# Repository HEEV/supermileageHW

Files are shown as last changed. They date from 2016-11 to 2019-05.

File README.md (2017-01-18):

# Cedarville Supermileage HW
Kicad files for PCBs on the Ceaderville Supermileage team. Also includes wiring diagrams and schematics
drawn in Kicad.
#Contents of Folders
* Library Folders
    * EllicottSamuel: Files I made before supermileage which were too much work to port over.
    *  parts_library: Files dedicated for the supermileage team.

* Project Folders
    * can_sensor: PCB to connect generic sensors to the CANBus.
    * current_sensor: Three port current sensor board that connects to the CANBus. 
	Current sensor chip is the Allegro ACS710.
    * pressure_sensor: Pressure sensor board, output as an analog voltage. 
	Supported sensors are the Honeywell ASDX100A24R, Honeywell HSCDRR004MD, and the
	AllSensors G4V-Mini.
    * Sting: wiring diagrams and schematics for Sting produced using Kicad.
        * wiring diagrams: kicad files for the wiring diagrams.
        * schematics: kicad files for the schematics.
    * Urbie: wiring diagrams and schematics for Urbie produced using Kicad.
    	* wiring diagrams: kicad files for the wiring diagrams.
        * schematics: kicad files for the schematics.

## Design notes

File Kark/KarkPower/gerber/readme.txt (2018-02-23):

readme.txt - KarkPower folder contents

KarkPower.drl            - Drill File
KarkPower-drl_map.pdf    - Drill Map File
KarkPower-B-Cu.gbl       - Back Copper
KarkPower-B-SilkS.gbo    - Back Silk
KarkPower-F-Cu.gtl       - Front Copper
KarkPower-F-SilkS.gto    - Front Silk
KarkPower-Edge-Cuts.gm1  - Board Edge

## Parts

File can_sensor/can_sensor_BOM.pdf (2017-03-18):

can_sensor_BOM

Page 1

Reference | Value | Footprint | Count | FootprintLib | Distributor | PN
C15;C5;C17;C13;C11 | 1uf | C_0603_HandSoldering | 5 Capacitors_SMD | | Mouser | 80-C0603C105K8P
C6;C16;C9;C10;C2;C8;C4;C18;C14;C12 | 0.1uf | C_0603_HandSoldering | 10 Capacitors_SMD
C7;C3;C1;C19;C20 | 10uf | C_0603_HandSoldering | 5 Capacitors_SMD | | Mouser | 80-C0603C105K8P
D1;D2;D3;D4 | hi_v | SOD-123 | 4 Diodes_SMD
D7 | reverse | SOD-123 | 1 Diodes_SMD | | Mouser | 581-SD1206S040S0R5
D8 | LED1 | LED_0603 | 1 LEDs
D9 | LED2 | LED_0603 | 1 LEDs
P1 | IO1 | Molex-duraClick-4conn | 1 User_Connectors | | Mouser | 538-53261-0471
P2 | IO2 | Molex-duraClick-4conn | 1 User_Connectors | | Mouser | 538-53261-0471
P4 | CONN_01X03 | Pin_Header_Straight_1x03 | 1 Pin_Headers
P5 | USB | USB_Micro-B | 1 Connect | | Mouser | 649-10118194-0001LF
P6 | CAN_IN | Molex-duraClick-4conn | 1 User_Connectors | | Mouser | 538-53261-0471
P7 | CAN_OUT | Molex-duraClick-4conn | 1 User_Connectors | | Mouser | 538-53261-0471
R1;R9;R8 | 100K | R_0603_HandSoldering | 3 Resistors_SMD | | Mouser | 71-CRCW0603-100K-E3
R10;R11;R12 | 120R | R_0603_HandSoldering | 3 Resistors_SMD | | Mouser | 71-CRCW0603-120-E3
R6;R5;R3;R2 | R | R_0603_HandSoldering | 4 Resistors_SMD
SW1 | RESET | SW_SPST_FSMSM | 1 Buttons_Switches_SMD
SW2 | BOOT | SW_SPST_FSMSM | 1 Buttons_Switches_SMD
U1 | NJM2870F0 | SOT-23-5 | 1 TO_SOT_Packages_SMD | | Mouser | 513-NJM2870F05-TE2
U2 | MIC5317 | SOT-23-5 | 1 TO_SOT_Packages_SMD | | Mouser | 998-MIC5317-3.3YM5TR
U3 | STM32F042C6 | TQFP-48_7x7mm_Pitch0.5mm | 1 Housings_QFP
U4 | mcp2562 | SOIC-8-N | 1 SMD_Packages | | Mouser | 579-MCP2562-E/SN

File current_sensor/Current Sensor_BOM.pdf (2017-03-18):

Current Sensor_BOM

Page 1

Reference | Value | Footprint | Count | FootprintLib | Distributor | PN
C1;C8;C14 | 1nf | C_0603_HandSoldering | 3 Capacitors_SMD
C23;C25;C21;C19 | 1uf | C_0603_HandSoldering | 4 Capacitors_SMD | | Mouser | 80-C0603C105K8P
C4;C5;C6;C3;C11;C16;C10;C13;C24;C18;C17;C26;C22;C20 | 0.1uf | C_0603_HandSoldering | 14 Capacitors_SMD
C7;C12 | 10uf | C_0603_HandSoldering | 2 Capacitors_SMD
C9;C15;C2 | 4.7nf | C_0603_HandSoldering | 3 Capacitors_SMD
D1 | LED1 | LED-3MM | 1 LEDs
D2 | LED2 | LED-3MM | 1 LEDs
D4;D3;D5;D7;D6;D8 | D_Schottky_Small | SOD-123 | 6 Diodes_SMD | | Mouser | 512-SS14FL
P1 | CAN_IN | Molex-duraClick-4conn | 1 User_Connectors | | Mouser | 538-502352-0400
P10;P11;P12 | CONN_02X03 | Pin_Header_Straight_2x03 | 3 Pin_Headers
P2 | CAN_OUT | Molex-duraClick-4conn | 1 User_Connectors | | Mouser | 538-502352-0400
P3 | DuraClik-5 | Molex-duraClick-5conn | 1 User_Connectors | | Mouser | 538-502352-0501
P4;P5;P6 | Ultra-Fit | Molex-UltraFit-2p | 3 Supermileage | | Mouser | 538-172310-2102
P7 | CONN_01X03 | Pin_Header_Straight_1x03 | 1 Pin_Headers
P8 | USB | USB_Micro-B | 1 Connect | | Mouser | 649-10118194-0001LF
P9 | CONN_01X02 | Pin_Header_Straight_1x02 | 1 Pin_Headers
Q1 | Reverse | SOT-23_Handsoldering | 1 TO_SOT_Packages_SMD | | Mouser | 863-NTR3A30PZT1G
R1;R3;R5 | 1k | R_0603_HandSoldering | 3 Resistors_SMD
R10;R22;R24 | 8k2 | R_0603_HandSoldering | 3 Resistors_SMD
R12;R18;R20 | 4k7 | R_0603_HandSoldering | 3 Resistors_SMD
R14;R7 | 100K | R_0603_HandSoldering | 2 Resistors_SMD | | Mouser | 71-CRCW0603-100K-E3
R15;R16;R17 | 120R | R_0603_HandSoldering | 3 Resistors_SMD | | Mouser | 71-CRCW0603-120-E3
R2;R4;R6 | 2k | R_0603_HandSoldering | 3 Resistors_SMD
R8;R26;R28 | 18k | R_0603_HandSoldering | 3 Resistors_SMD | | Mouser
R9;R11;R13;R27;R23;R19;R29;R25;R21 | 1k3 | R_0603_HandSoldering | 9 Resistors_SMD
SW1 | RESET | SW_PUSH_6mm | 1 Buttons_Switches_ThroughHole | | Mouser | SKHHPPA010
SW2 | BOOT | SW_PUSH_6mm | 1 Buttons_Switches_ThroughHole | | Mouser | SKHHPPA010
U1;U3;U5 | ACS710 | DIP-16-SchmartBoard | 3 Supermileage
U2 | NJM2870F0 | SOT-23-5 | 1 TO_SOT_Packages_SMD | | Mouser | 513-NJM2870F05-TE2
U4 | MIC5317 | SOT-23-5 | 1 TO_SOT_Packages_SMD | | Mouser | 998-MIC5317-3.3YM5TR
U6 | STM32F042C6 | TQFP-48_7x7mm_Pitch0.5mm | 1 Housings_QFP | | Mouser | 511-STM32F042C6T6
U7 | mcp2562 | SOIC-8-N | 1 SMD_Packages | | Mouser | 579-MCP2562-E/SN

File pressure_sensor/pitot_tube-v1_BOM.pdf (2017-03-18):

pitot_tube-v1_BOM

Page 1

Reference | Value | Footprint | Count | FootprintLib | Distributor
C1;C3;C4;C5;C7 | 0.1uf | C_0603_HandSoldering | 5 Capacitors_SMD | | Mouser
C2;C6;C8 | 10uf | C_0603_HandSoldering | 3 Capacitors_SMD
P1 | CONN_01X04 | Molex-duraClick-4conn | 1 User_Connectors
P2 | CONN_01X03 | Pin_Header_Straight_1x03 | 1 Pin_Headers
Q1;Q2 | Q_PMOS_GSD | SOT-23_Handsoldering | 2 TO_SOT_Packages_SMD
R1 | 1k | R_0603_HandSoldering | 1 Resistors_SMD
R2 | 2k | R_0603_HandSoldering | 1 Resistors_SMD
U1 | HSCDRR004MD | DIP-8 | 1supermileage
U2 | NJM2870F0 | SOT-23-5 | 1 TO_SOT_Packages_SMD
U3 | ASDX100A24R | ASDX100A24R | 1supermileage
U4 | G4V-MINI | Socket_Strip_Straight_1x04 | 1 Socket_Strips
W1;W2;W3;W4 | Mount | MountingHole_2.2mm_M2 | 4 Mounting_Holes

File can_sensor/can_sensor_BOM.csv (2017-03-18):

Reference | Value | Footprint | Count | Datasheet | FootprintLib | Distributor | PN
U4 | mcp2562 | SOIC-8-N | 1 |  | SMD_Packages | Mouser | 579-MCP2562-E/SN
U2 | MIC5317 | SOT-23-5 | 1 |  | TO_SOT_Packages_SMD | Mouser | 998-MIC5317-3.3YM5TR
C7;C3;C1;C19;C20 | 10uf | C_0603_HandSoldering | 5 |  | Capacitors_SMD | Mouser | 80-C0603C105K8P
C6;C16;C9;C10;C2;C8;C4;C18;C14;C12 | 0.1uf | C_0603_HandSoldering | 10 |  | Capacitors_SMD
C15;C5;C17;C13;C11 | 1uf | C_0603_HandSoldering | 5 |  | Capacitors_SMD | Mouser | 80-C0603C105K8P
D7 | reverse | SOD-123 | 1 |  | Diodes_SMD | Mouser | 581-SD1206S040S0R5
P6 | CAN_IN | Molex-duraClick-4conn | 1 |  | User_Connectors | Mouser | 538-53261-0471
P7 | CAN_OUT | Molex-duraClick-4conn | 1 |  | User_Connectors | Mouser | 538-53261-0471
P1 | IO1 | Molex-duraClick-4conn | 1 |  | User_Connectors | Mouser | 538-53261-0471
P2 | IO2 | Molex-duraClick-4conn | 1 |  | User_Connectors | Mouser | 538-53261-0471
R10;R11;R12 | 120R | R_0603_HandSoldering | 3 |  | Resistors_SMD | Mouser | 71-CRCW0603-120-E3
D8 | LED1 | LED_0603 | 1 |  | LEDs
D9 | LED2 | LED_0603 | 1 |  | LEDs
P5 | USB | USB_Micro-B | 1 |  | Connect | Mouser | 649-10118194-0001LF
SW2 | BOOT | SW_SPST_FSMSM | 1 |  | Buttons_Switches_SMD
SW1 | RESET | SW_SPST_FSMSM | 1 |  | Buttons_Switches_SMD
U1 | NJM2870F0 | SOT-23-5 | 1 |  | TO_SOT_Packages_SMD | Mouser | 513-NJM2870F05-TE2
R1;R9;R8 | 100K | R_0603_HandSoldering | 3 |  | Resistors_SMD | Mouser | 71-CRCW0603-100K-E3
P4 | CONN_01X03 | Pin_Header_Straight_1x03 | 1 |  | Pin_Headers
D1;D2;D3;D4 | hi_v | SOD-123 | 4 |  | Diodes_SMD
R6;R5;R3;R2 | R | R_0603_HandSoldering | 4 |  | Resistors_SMD
U3 | STM32F042C6 | TQFP-48_7x7mm_Pitch0.5mm | 1 |  | Housings_QFP

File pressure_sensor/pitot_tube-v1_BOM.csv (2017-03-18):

Reference | Value | Footprint | Count | Datasheet | FootprintLib | Distributor
U1 | HSCDRR004MD | DIP-8 | 1 |  | supermileage
P1 | CONN_01X04 | Molex-duraClick-4conn | 1 |  | User_Connectors
C1;C3;C4;C5;C7 | 0.1uf | C_0603_HandSoldering | 5 |  | Capacitors_SMD | Mouser
C2;C6;C8 | 10uf | C_0603_HandSoldering | 3 |  | Capacitors_SMD
W1;W2;W3;W4 | Mount | MountingHole_2.2mm_M2 | 4 |  | Mounting_Holes
U2 | NJM2870F0 | SOT-23-5 | 1 |  | TO_SOT_Packages_SMD
P2 | CONN_01X03 | Pin_Header_Straight_1x03 | 1 |  | Pin_Headers
R1 | 1k | R_0603_HandSoldering | 1 |  | Resistors_SMD
R2 | 2k | R_0603_HandSoldering | 1 |  | Resistors_SMD
Q1;Q2 | Q_PMOS_GSD | SOT-23_Handsoldering | 2 |  | TO_SOT_Packages_SMD
U3 | ASDX100A24R | ASDX100A24R | 1 |  | supermileage
U4 | G4V-MINI | Socket_Strip_Straight_1x04 | 1 |  | Socket_Strips

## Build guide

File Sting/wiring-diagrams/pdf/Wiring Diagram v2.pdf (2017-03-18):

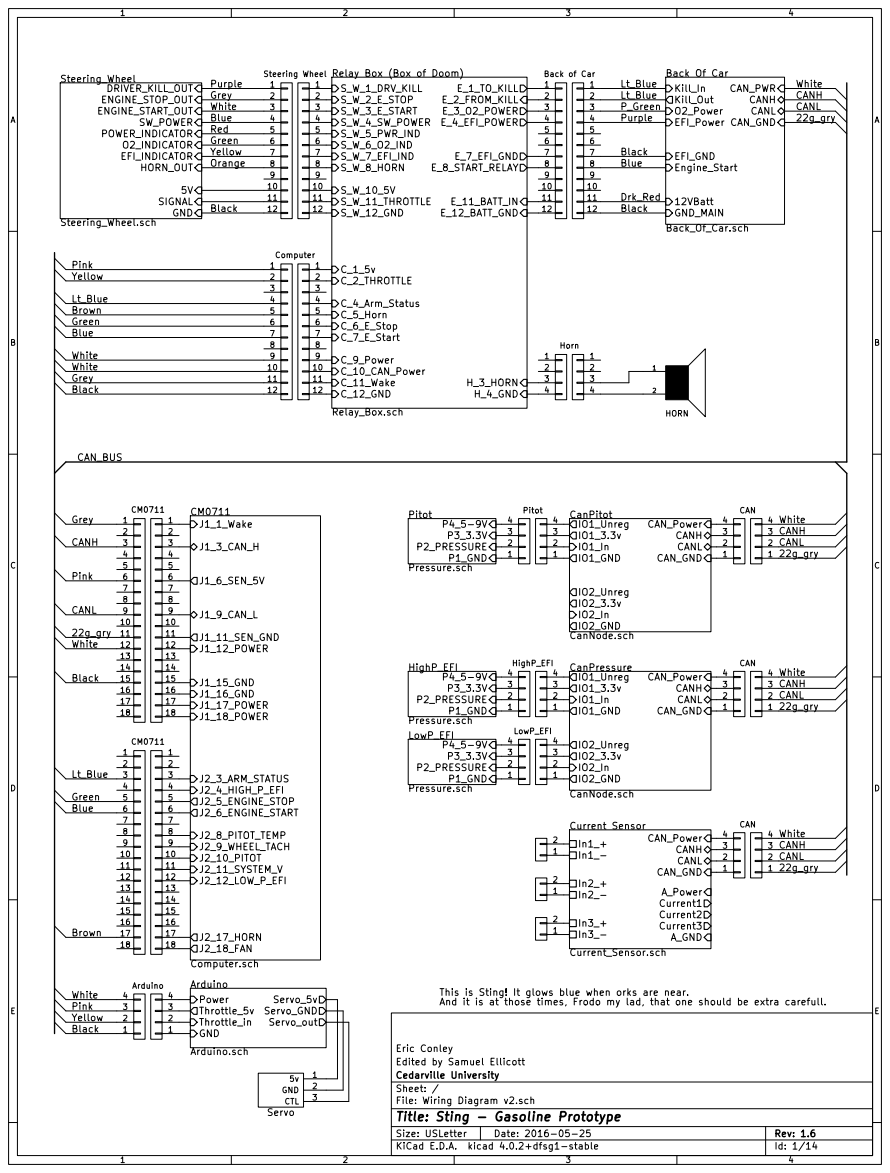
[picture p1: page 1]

2 | | 2 | | 2 | | 2 | Lt_Blue
3 | | 3 | | 3 | | 3 P_Green

C_10_CAN_Power Grey Pink Lt_Blue Brown Black White White Green Blue Yellow Grey White

10 | 2
11 | 3 | 3
12 | 4

12
13

This is Sting! It glows blue when orks are near.
And it is at those times, Frodo my lad, that one should be extra carefull.

Eric Conley
Edited by Samuel Ellicott
File: Wiring Diagram v2.sch Sheet: / Cedarville University

Id: 1/14 Title: Sting - Gasoline Prototype

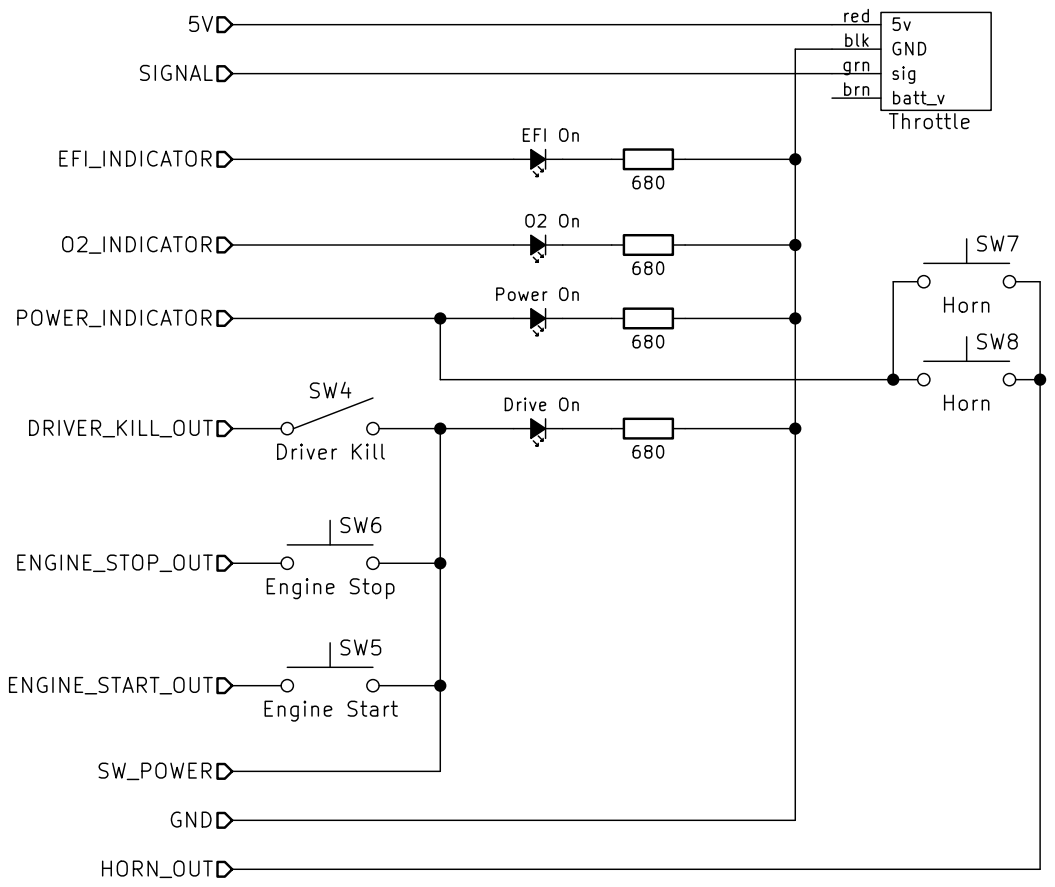
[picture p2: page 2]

Eric Conley
Edited by Samuel Ellicott
Cedarville University
Sheet: /Steering_Wheel/
File: Steering_Wheel.sch
Id: 2/14 Title: Sting - Gasoline Prototype

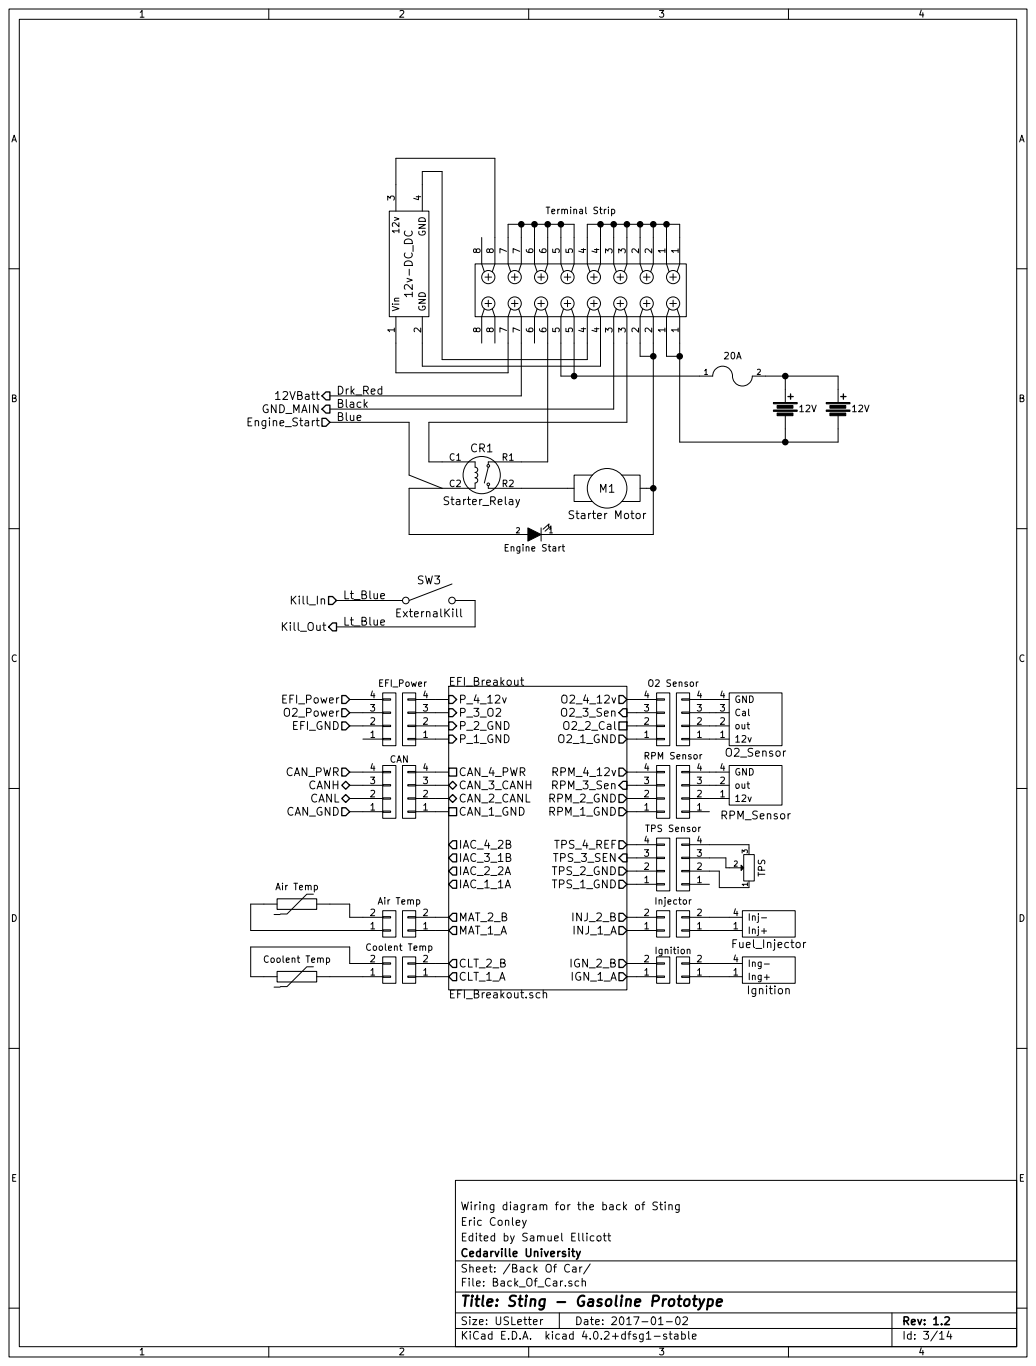
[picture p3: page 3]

Wiring diagram for the back of Sting
Eric Conley
Edited by Samuel Ellicott
File: Back_Of_Car.sch Sheet: /Back Of Car/ Cedarville University

Id: 3/14 Title: Sting - Gasoline Prototype

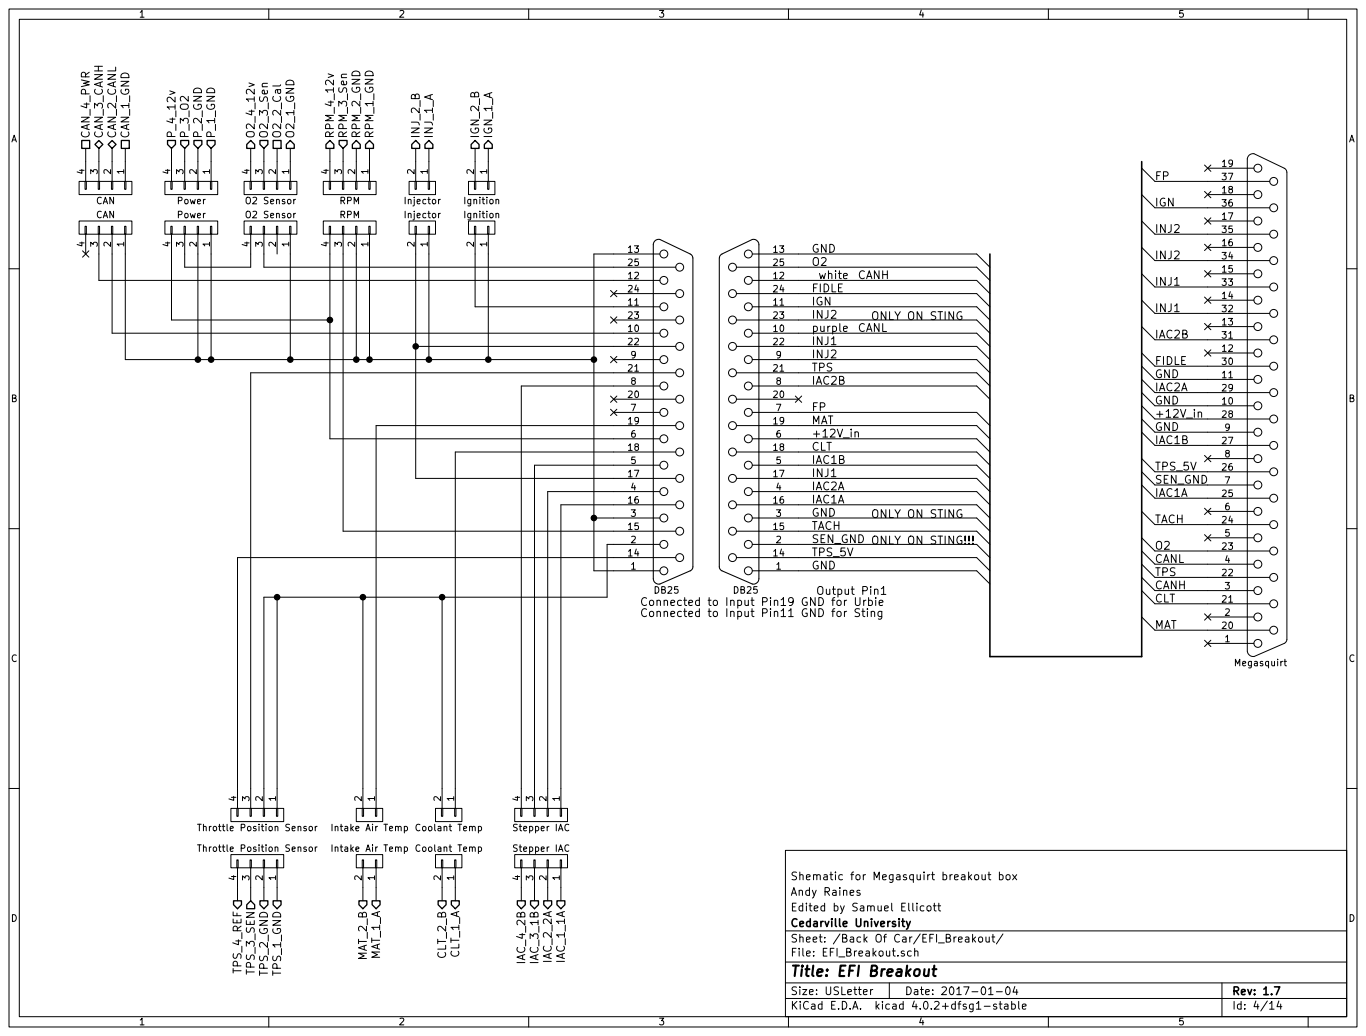
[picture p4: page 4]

1 Coolant Temp MAT CLT

Connected to Input Pin19 GND for Urbie
Connected to Input Pin11 GND for Sting

Shematic for Megasquirt breakout box
Andy Raines
Edited by Samuel Ellicott
Cedarville University
Sheet: /Back Of Car/EFI_Breakout/
File: EFI_Breakout.sch
Id: 4/14 Title: EFI Breakout

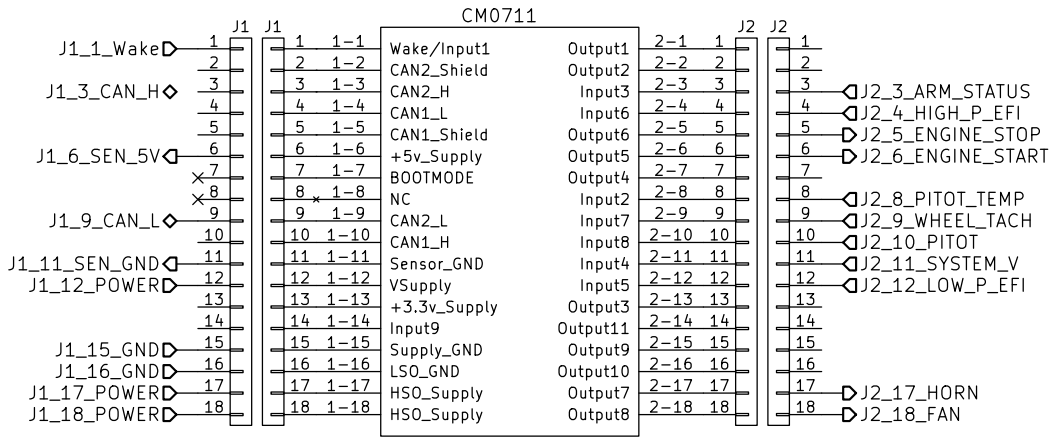
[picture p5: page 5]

10 | 10
11 | 11
12 | 12
13 | 13
14 | 14

16 | 16
17 | 17
18 | 18

CM0711 Computer sheet Samuel Ellicott

File: Computer.sch Sheet: /CM0711/ Cedarville University

Id: 5/14 Title: Sting - Gasoline Prototype

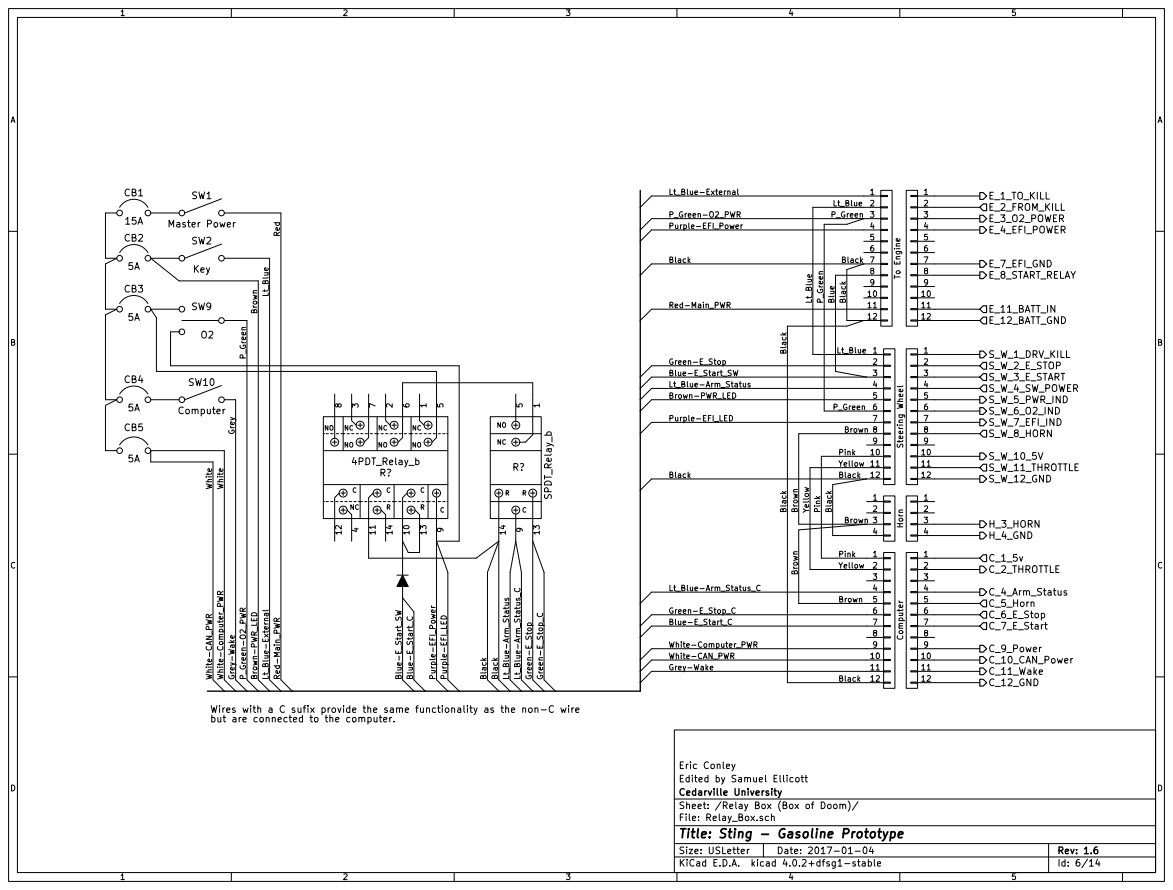
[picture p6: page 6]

Purple-EFI_Power Black Red-Main_PWR Green-E_Stop Blue-E_Start_SW

Blue-E_Start_C White-Computer_PWR White-CAN_PWR Grey-Wake

but are connected to the computer.

Eric Conley
Edited by Samuel Ellicott
Cedarville University
Sheet: /Relay Box (Box of Doom)/
File: Relay_Box.sch
Id: 6/14 Title: Sting - Gasoline Prototype

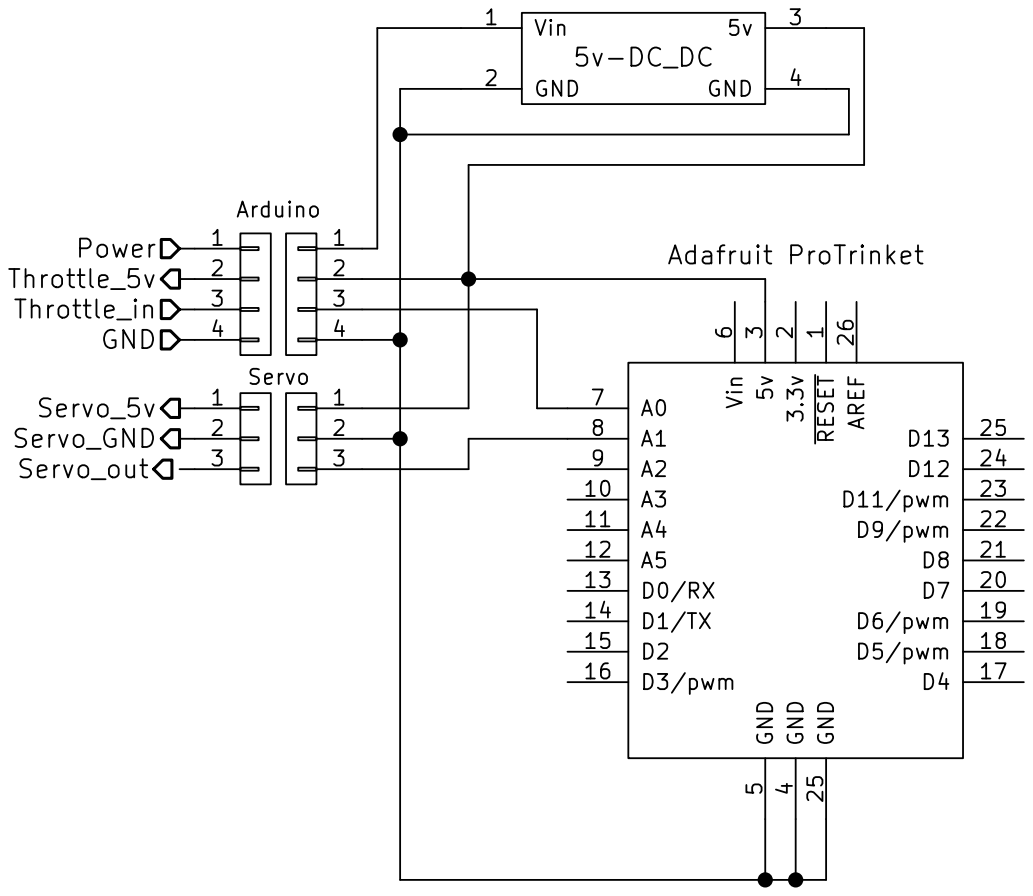
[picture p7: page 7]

6 A0 7 A1 8 A2 9 A3 10 D7 20 A4 11 D8 21 A5 12 D9/pwm 22 D0/RX 13 D11/pwm 23 D1/TX 14 D12 24 D2 15 D13 25 GND 25

1 3.3v 2 5v 3 GND
Id: 7/14 Title: Arduino Breakout File: Arduino.sch Sheet: /Arduino/ Cedarville University Samuel Ellicott RESET

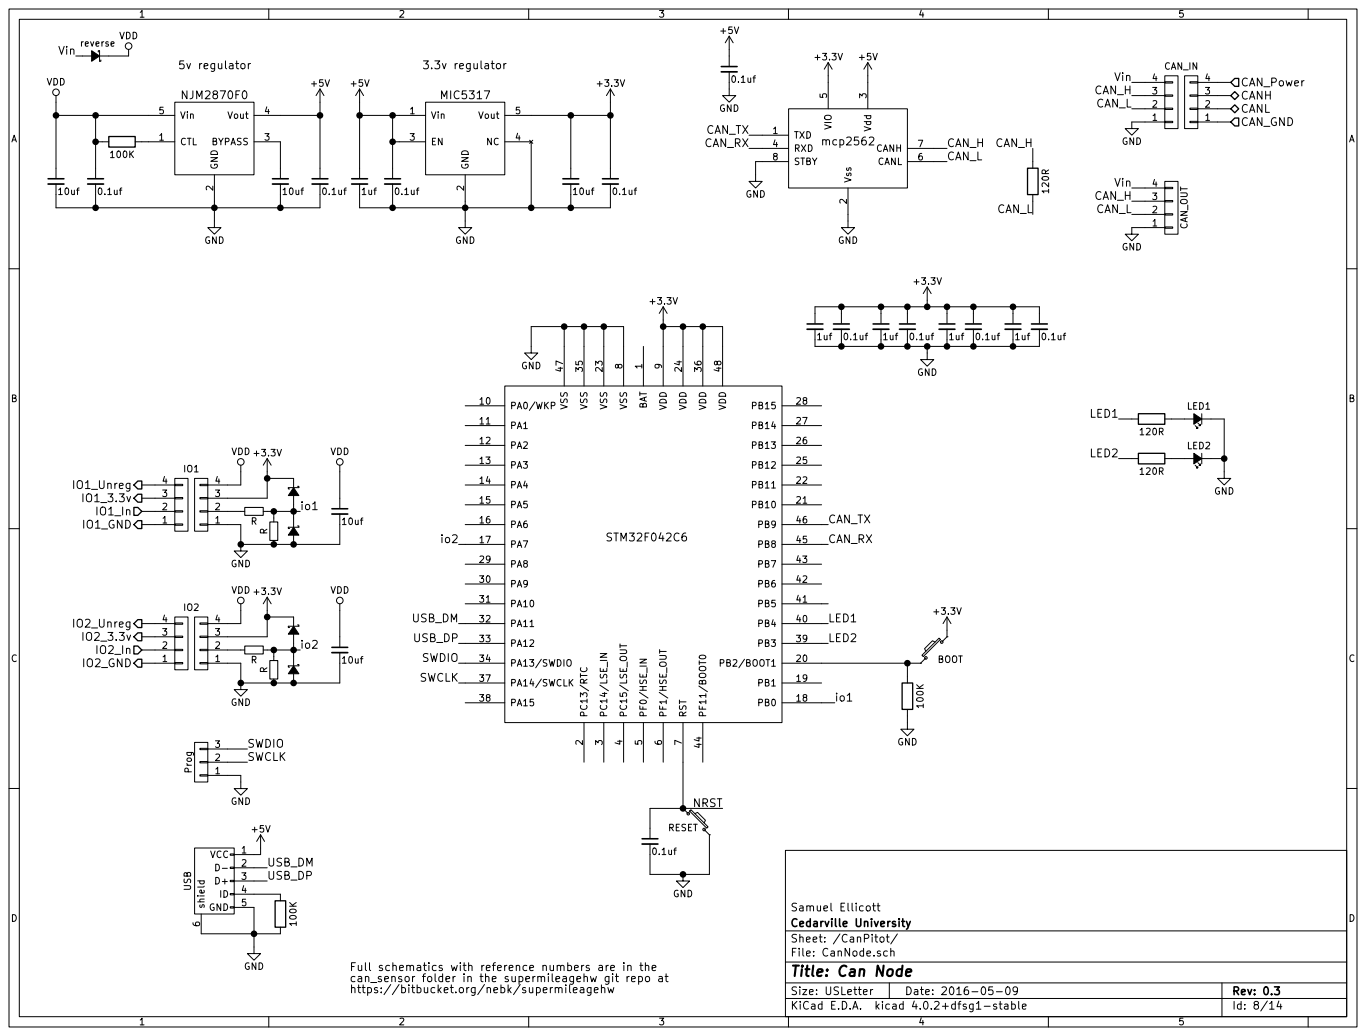
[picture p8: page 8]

9 PA0/WKP 10 PB2/BOOT1 20 PA9 30 PB4 40 PA1 11 PB10 21 PA10 31 PB5 41 PA2 12 PB11 22 PA11 32 PB6 42 PA3 13 VSS 23 PA12 33 PB7 43 PA4 14 VDD 24 PA13/SWDIO 34 PF11/BOOT0 44 PA5 15 PB12 25 VSS 35 PB8 45 PA6 16 PB13 26 VDD 36 PB9 46 PA7 17 PB14 27 PA14/SWCLK 37 VSS 47 PB0 18 PB15 28 PA15 38 VDD 48 PB1 19 PA8 29 PB3 39 STM32F042C6

File: CanNode.sch Sheet: /CanPitot/ Cedarville University Samuel Ellicott

Full schematics with reference numbers are in the can_sensor folder in the supermileagehw git repo at
https://bitbucket.org/nebk/supermileagehw

Id: 8/14 Title: Can Node

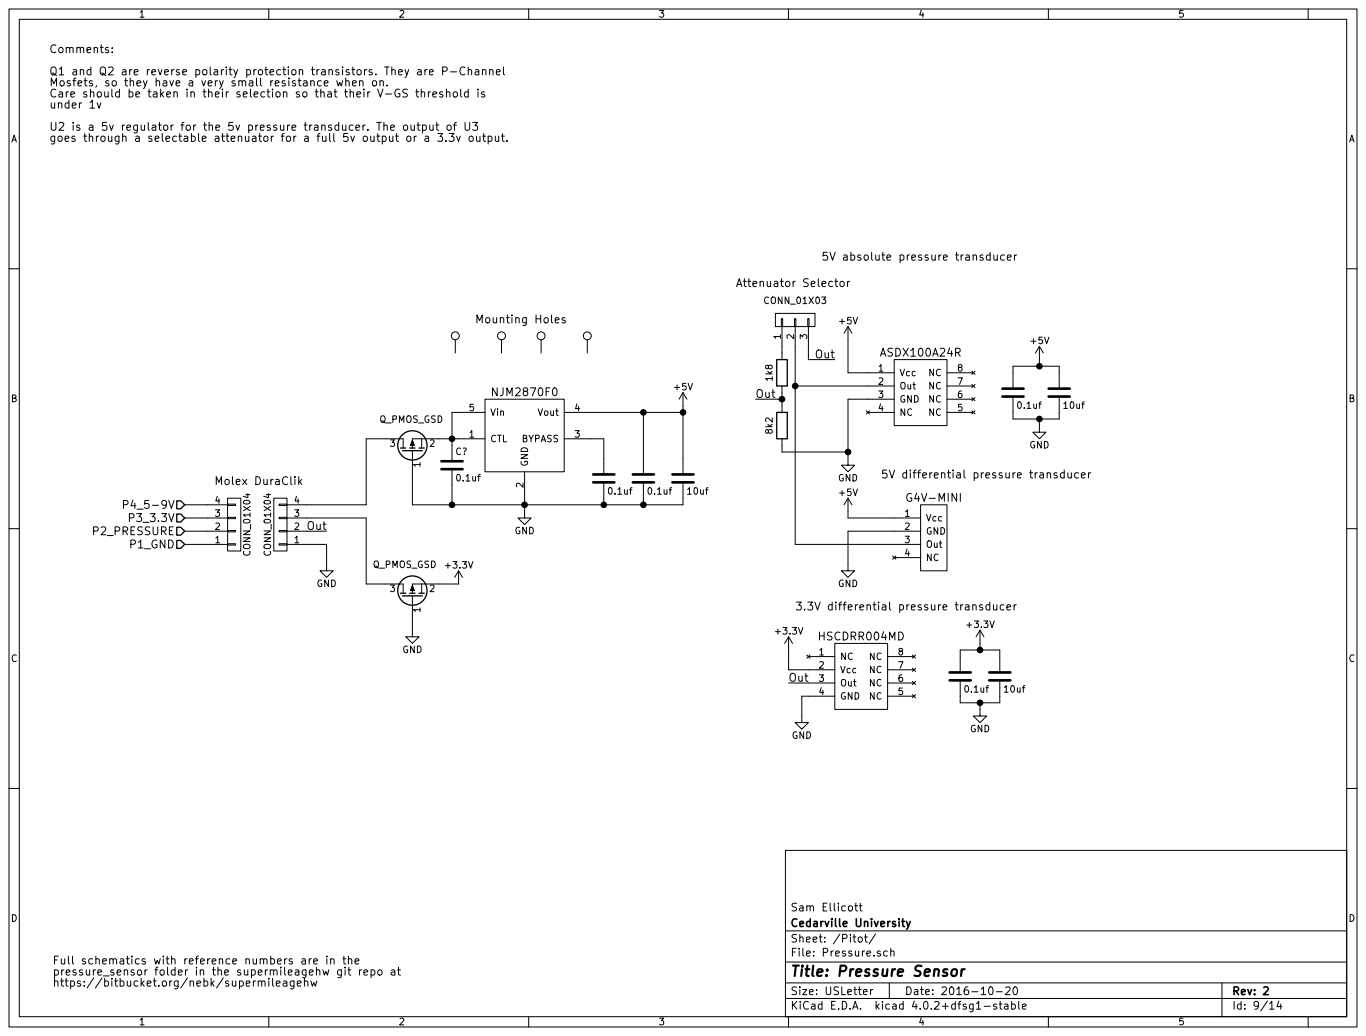
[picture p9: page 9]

Comments:
Q1 and Q2 are reverse polarity protection transistors. They are P-Channel
Mosfets, so they have a very small resistance when on.
Care should be taken in their selection so that their V-GS threshold is under 1v U2 is a 5v regulator for the 5v pressure transducer. The output of U3

goes through a selectable attenuator for a full 5v output or a 3.3v output.

Full schematics with reference numbers are in the pressure_sensor folder in the supermileagehw git repo at
https://bitbucket.org/nebk/supermileagehw

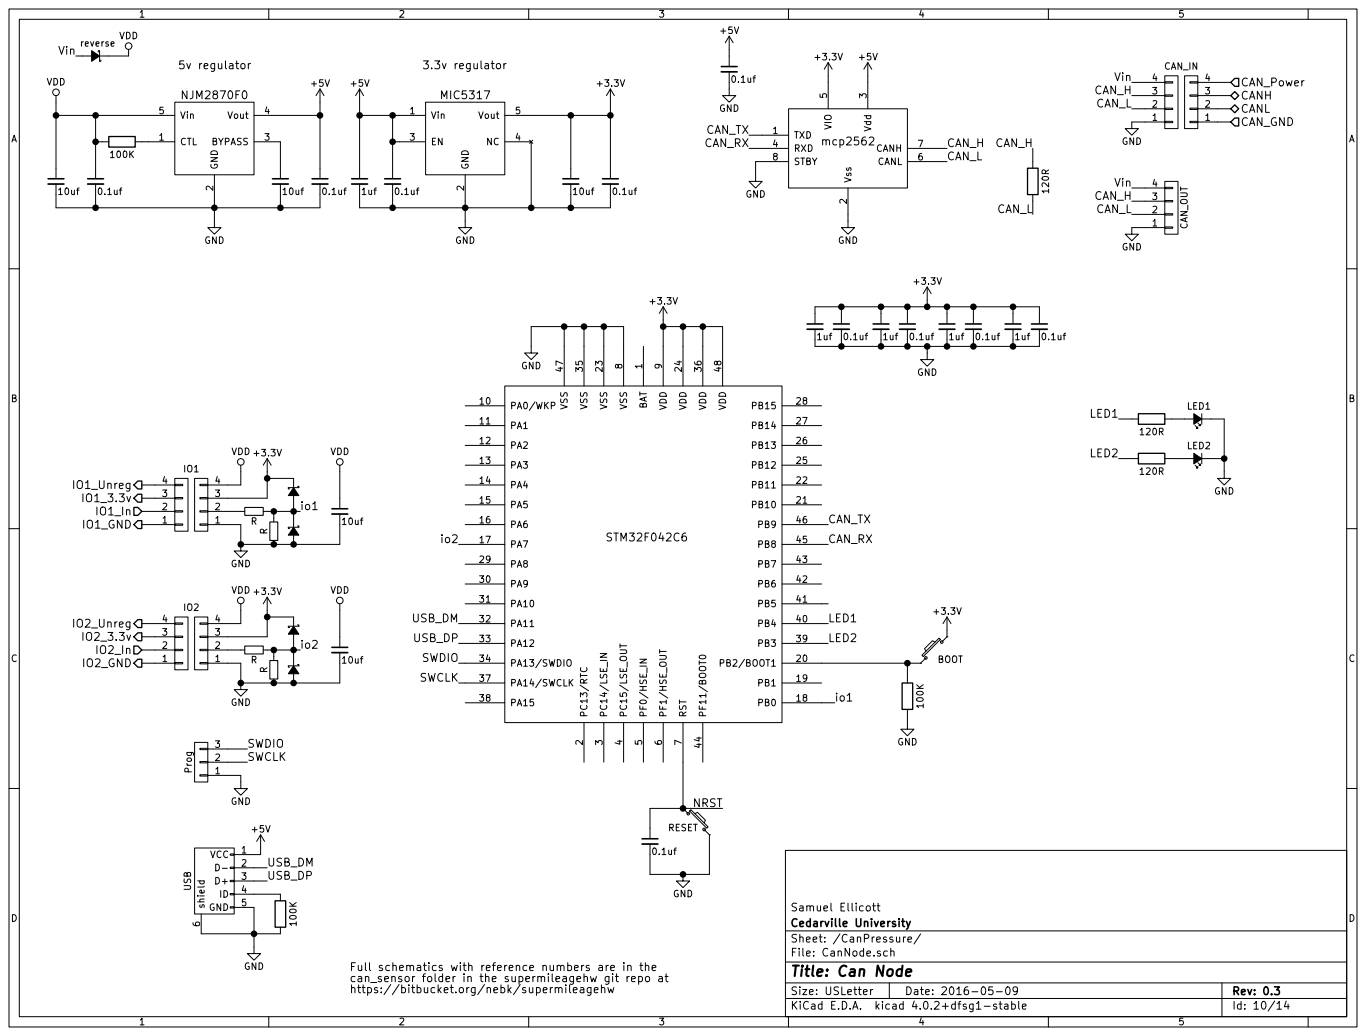
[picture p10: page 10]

9 PA0/WKP 10 PB2/BOOT1 20 PA9 30 PB4 40 PA1 11 PB10 21 PA10 31 PB5 41 PA2 12 PB11 22 PA11 32 PB6 42 PA3 13 VSS 23 PA12 33 PB7 43 PA4 14 VDD 24 PA13/SWDIO 34 PF11/BOOT0 44 PA5 15 PB12 25 VSS 35 PB8 45 PA6 16 PB13 26 VDD 36 PB9 46 PA7 17 PB14 27 PA14/SWCLK 37 VSS 47 PB0 18 PB15 28 PA15 38 VDD 48 PB1 19 PA8 29 PB3 39 STM32F042C6

File: CanNode.sch Sheet: /CanPressure/ Cedarville University Samuel Ellicott

Full schematics with reference numbers are in the can_sensor folder in the supermileagehw git repo at
https://bitbucket.org/nebk/supermileagehw

Id: 10/14 Title: Can Node

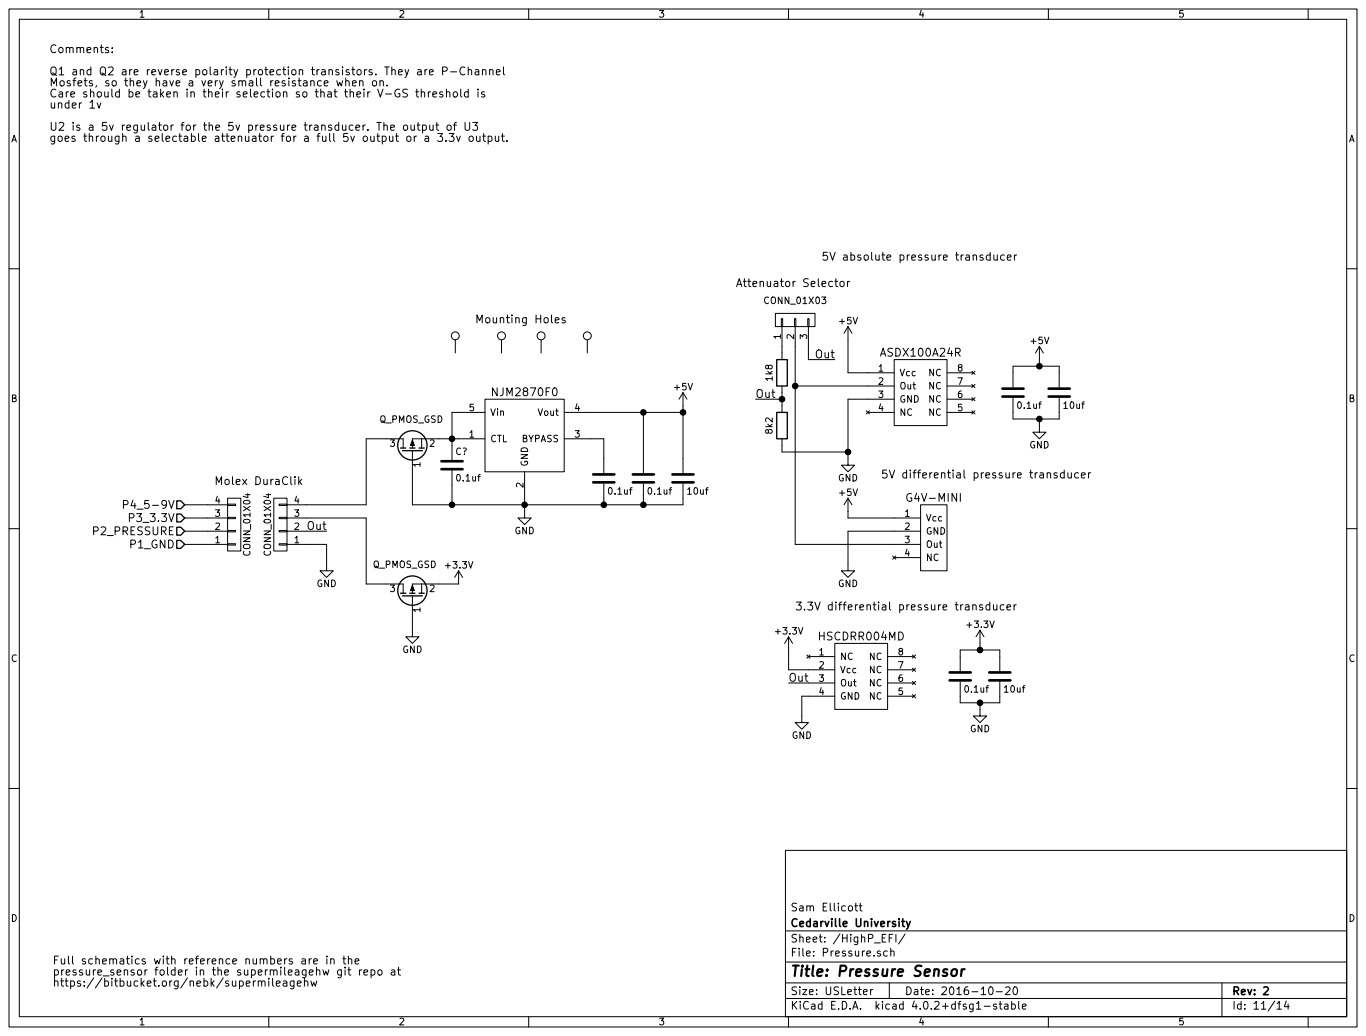
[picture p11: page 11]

Comments:
Q1 and Q2 are reverse polarity protection transistors. They are P-Channel
Mosfets, so they have a very small resistance when on.
Care should be taken in their selection so that their V-GS threshold is under 1v U2 is a 5v regulator for the 5v pressure transducer. The output of U3

goes through a selectable attenuator for a full 5v output or a 3.3v output.

Id: 11/14 Title: Pressure Sensor File: Pressure.sch Sheet: /HighP_EFI/

Full schematics with reference numbers are in the pressure_sensor folder in the supermileagehw git repo at
https://bitbucket.org/nebk/supermileagehw

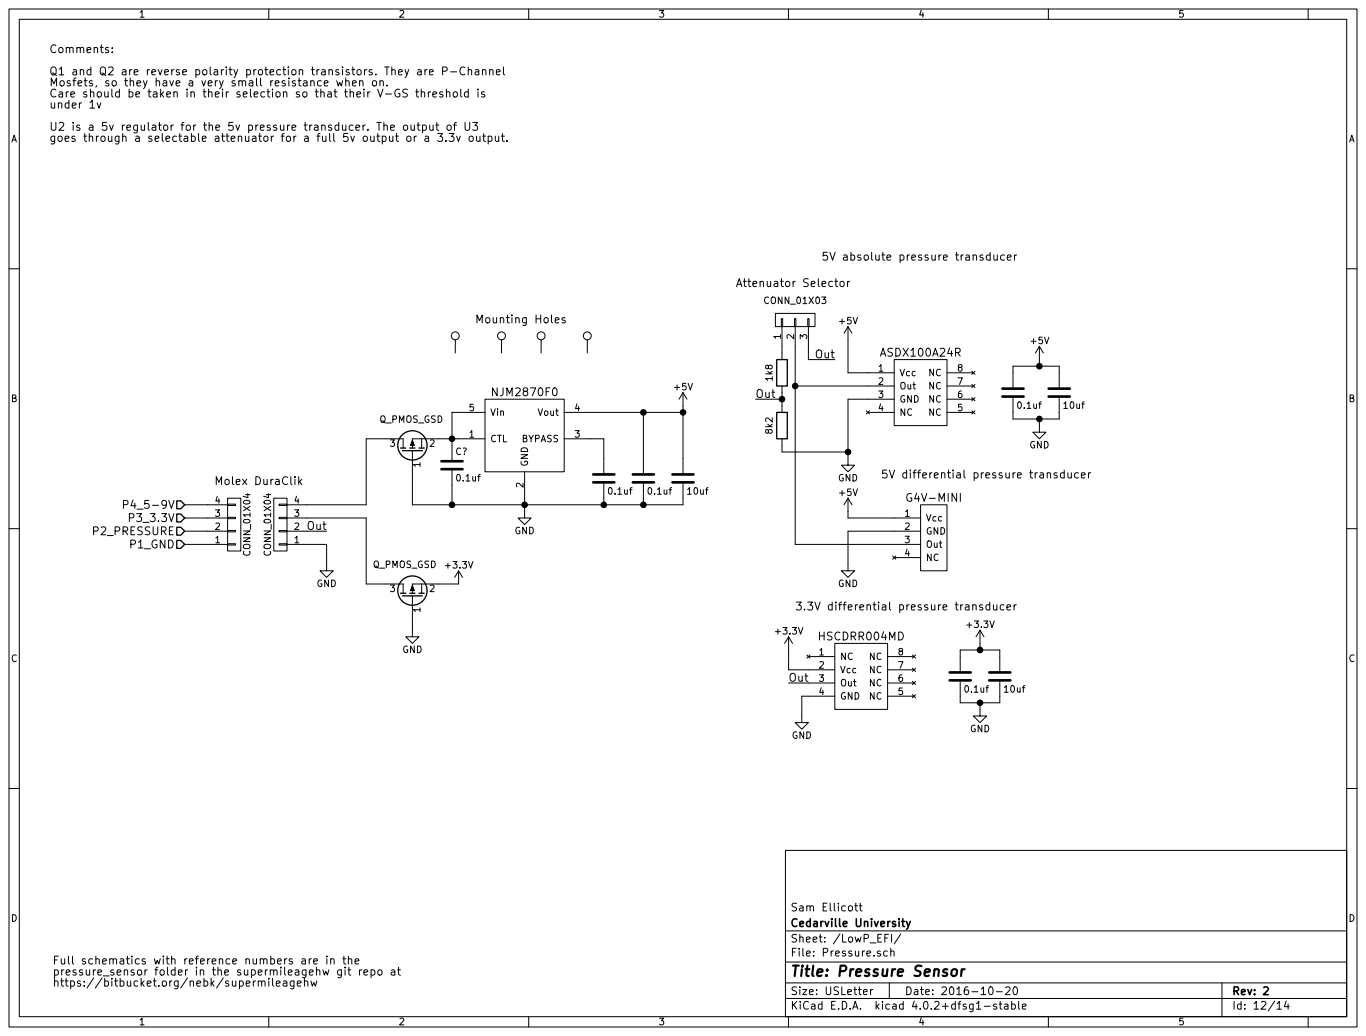
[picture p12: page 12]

Comments:
Q1 and Q2 are reverse polarity protection transistors. They are P-Channel
Mosfets, so they have a very small resistance when on.
Care should be taken in their selection so that their V-GS threshold is under 1v U2 is a 5v regulator for the 5v pressure transducer. The output of U3

goes through a selectable attenuator for a full 5v output or a 3.3v output.

Id: 12/14 Title: Pressure Sensor File: Pressure.sch Sheet: /LowP_EFI/

Full schematics with reference numbers are in the pressure_sensor folder in the supermileagehw git repo at
https://bitbucket.org/nebk/supermileagehw

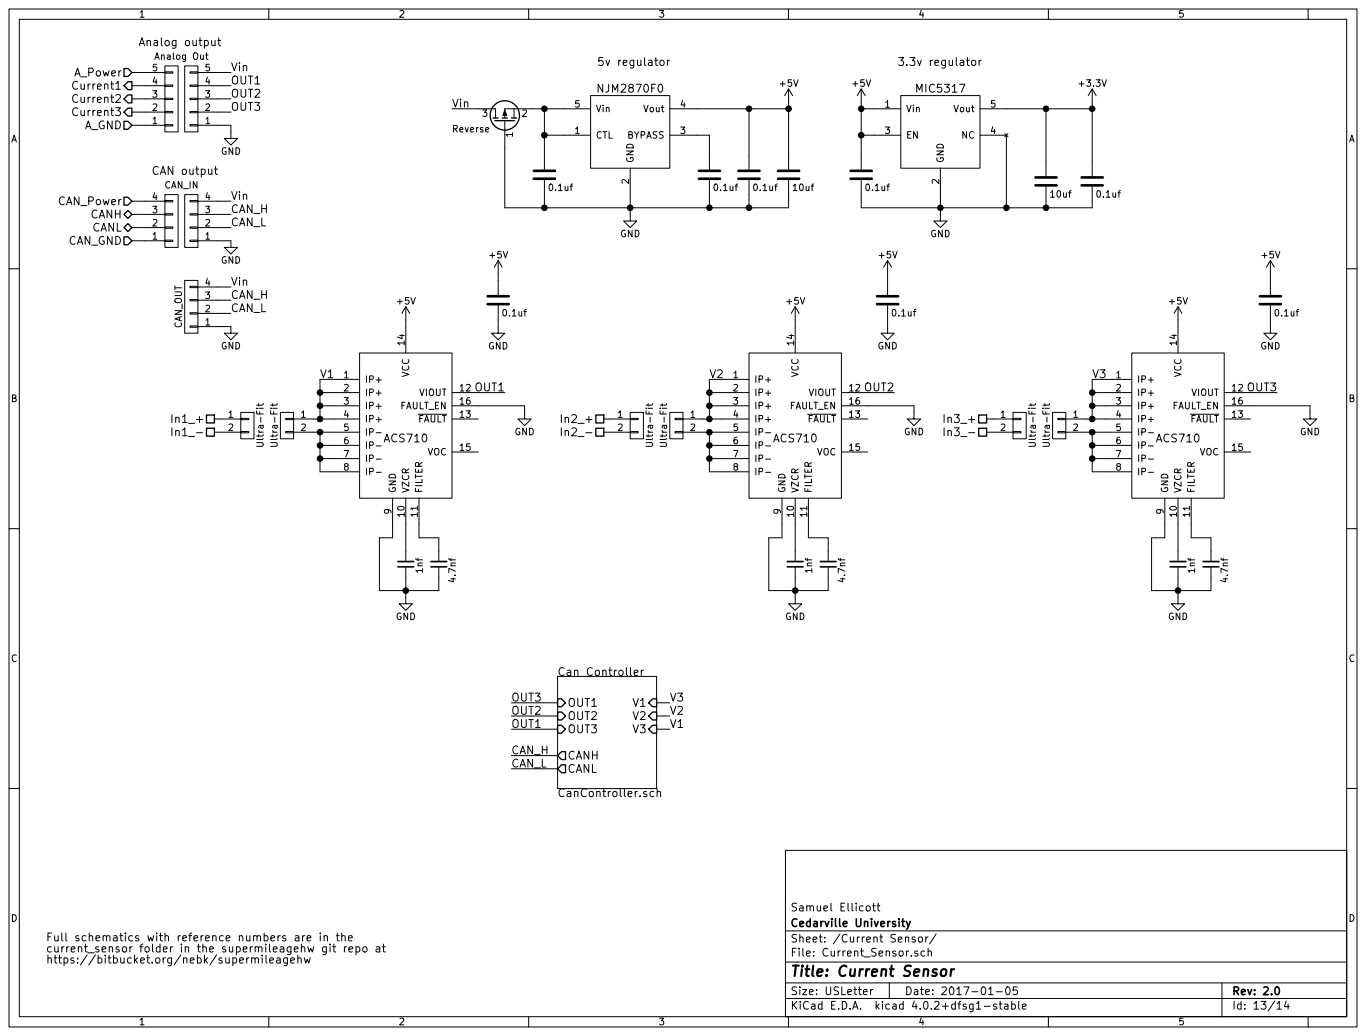
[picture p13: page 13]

9 VZCR 10 FILTER 11 VIOUT 12 FAULT 13 VCC 14 VOC 15 FAULT_EN 16 ACS710 GND OUT1

9 VZCR 10 FILTER 11 VIOUT 12 FAULT 13 VCC 14 VOC 15 FAULT_EN 16 ACS710 4.7nf GND OUT2

9 VZCR 10 FILTER 11 VIOUT 12 FAULT 13 VCC 14 VOC 15 FAULT_EN 16 ACS710 4.7nf GND OUT3

File: Current_Sensor.sch Sheet: /Current Sensor/ Cedarville University Samuel Ellicott

Full schematics with reference numbers are in the current_sensor folder in the supermileagehw git repo at
https://bitbucket.org/nebk/supermileagehw

Id: 13/14 Title: Current Sensor

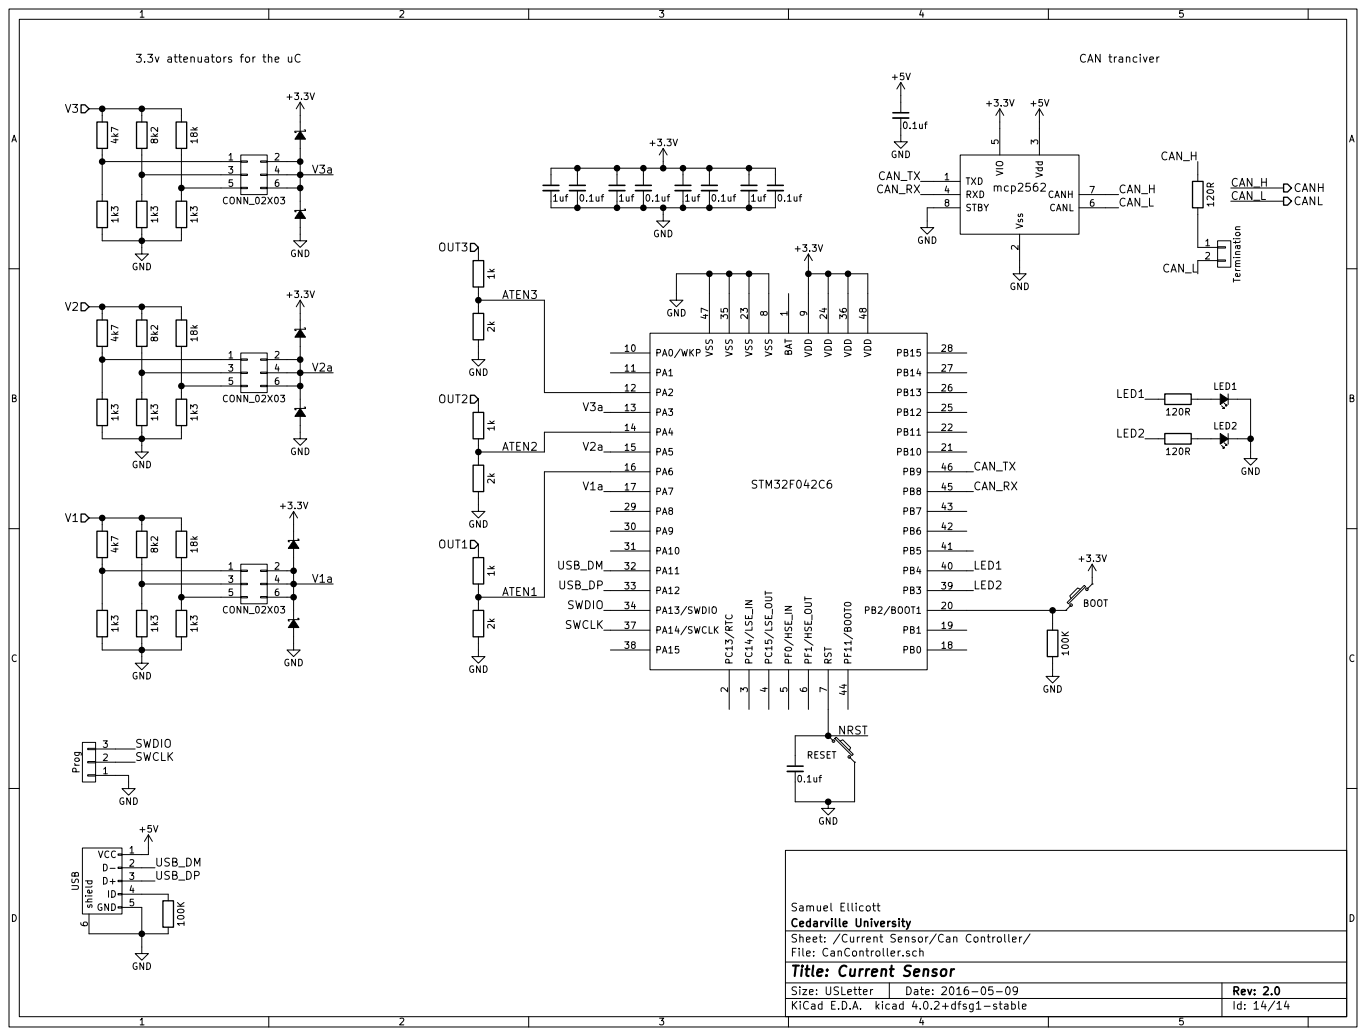
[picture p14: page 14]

3.3v attenuators for the uC

9 PA0/WKP 10 PB2/BOOT1 20 PA9 30 PB4 40 PA1 11 PB10 21 PA10 31 PB5 41 PA2 12 PB11 22 PA11 32 PB6 42 PA3 13 VSS 23 PA12 33 PB7 43 PA4 14 VDD 24 PA13/SWDIO 34 PF11/BOOT0 44 PA5 15 PB12 25 VSS 35 PB8 45 PA6 16 PB13 26 VDD 36 PB9 46 PA7 17 PB14 27 PA14/SWCLK 37 VSS 47 PB0 18 PB15 28 PA15 38 VDD 48 PB1 19 PA8 29 PB3 39 STM32F042C6

Id: 14/14 Title: Current Sensor File: CanController.sch Sheet: /Current Sensor/Can Controller/ Cedarville University Samuel Ellicott

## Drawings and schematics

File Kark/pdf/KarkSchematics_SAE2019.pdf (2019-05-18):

# 15A CB102

1 | 2 SW101 Master Power 1 | 2 SW102

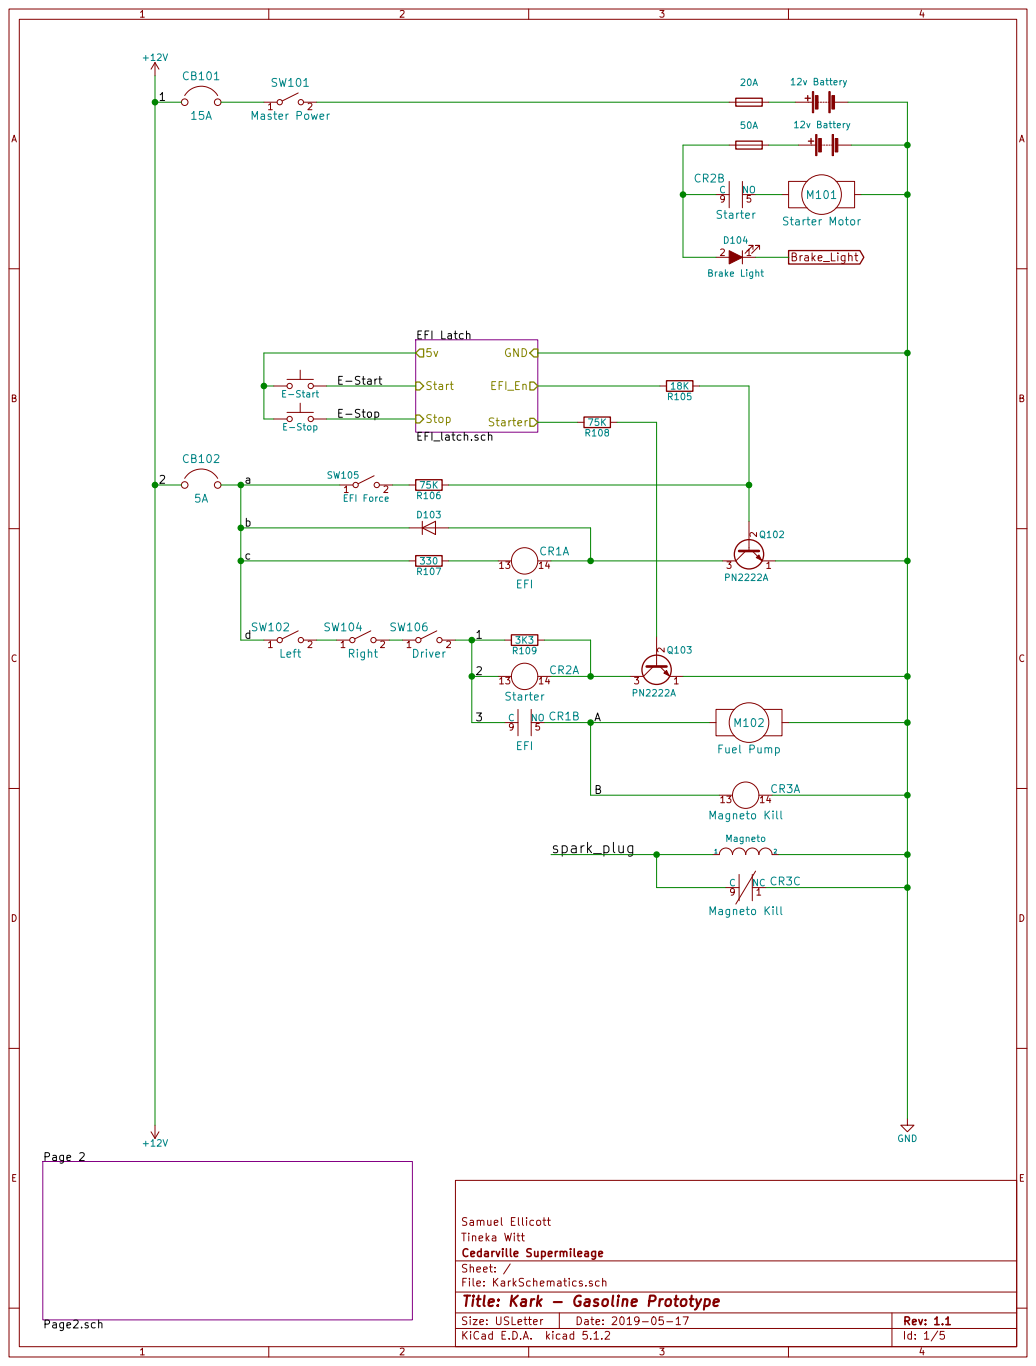
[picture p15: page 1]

File: KarkSchematics.sch Sheet: / Cedarville Supermileage Tineka Witt Samuel Ellicott

Id: 1/5 Title: Kark - Gasoline Prototype

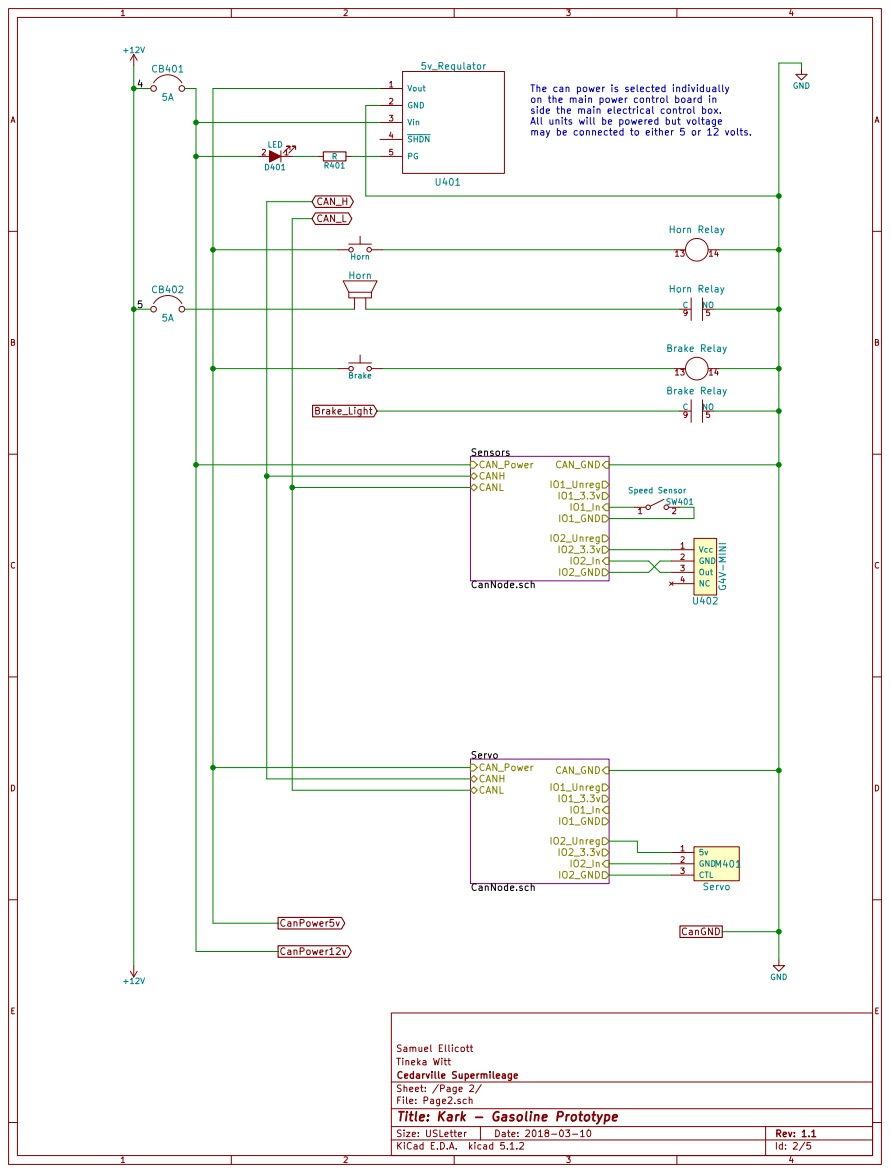
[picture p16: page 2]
E Date: 2018-03-10 KiCad E.D.A. kicad 5.1.2 Size: USLetter; Rev: 1.1; GND +12V; GND CAN_H; CAN_L; Vout 1; GND 2; Vin 3; SHDN 4; 5v_Regulator 5A; CanPower12v; CanPower5v; CanGND; The can power is selected individually; Sensors; CanNode.sch; CAN_Power CANH CANL; CAN_GND; IO1_Unreg; IO2_Unreg; IO1_In IO1_GND; IO2_In IO2_GND; Vcc 1; Out 3; NC 4 U402 G⁴V⁻MINI 1; 2SW401 Speed Sensor Horn CB402; Brake_Light; Servo; CTL 3; M401 Servo; LED; Horn; 14 Horn Relay NO; 9 Horn Relay Brake; 14 Brake Relay NO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

on the main power control board in side the main electrical control box. All units will be powered but voltage

may be connected to either 5 or 12 volts.

Cedarville Supermileage Tineka Witt Samuel Ellicott

Sheet: /Page 2/
File: Page2.sch
Id: 2/5 Title: Kark - Gasoline Prototype

# 1u +5V GND EFI Latch System

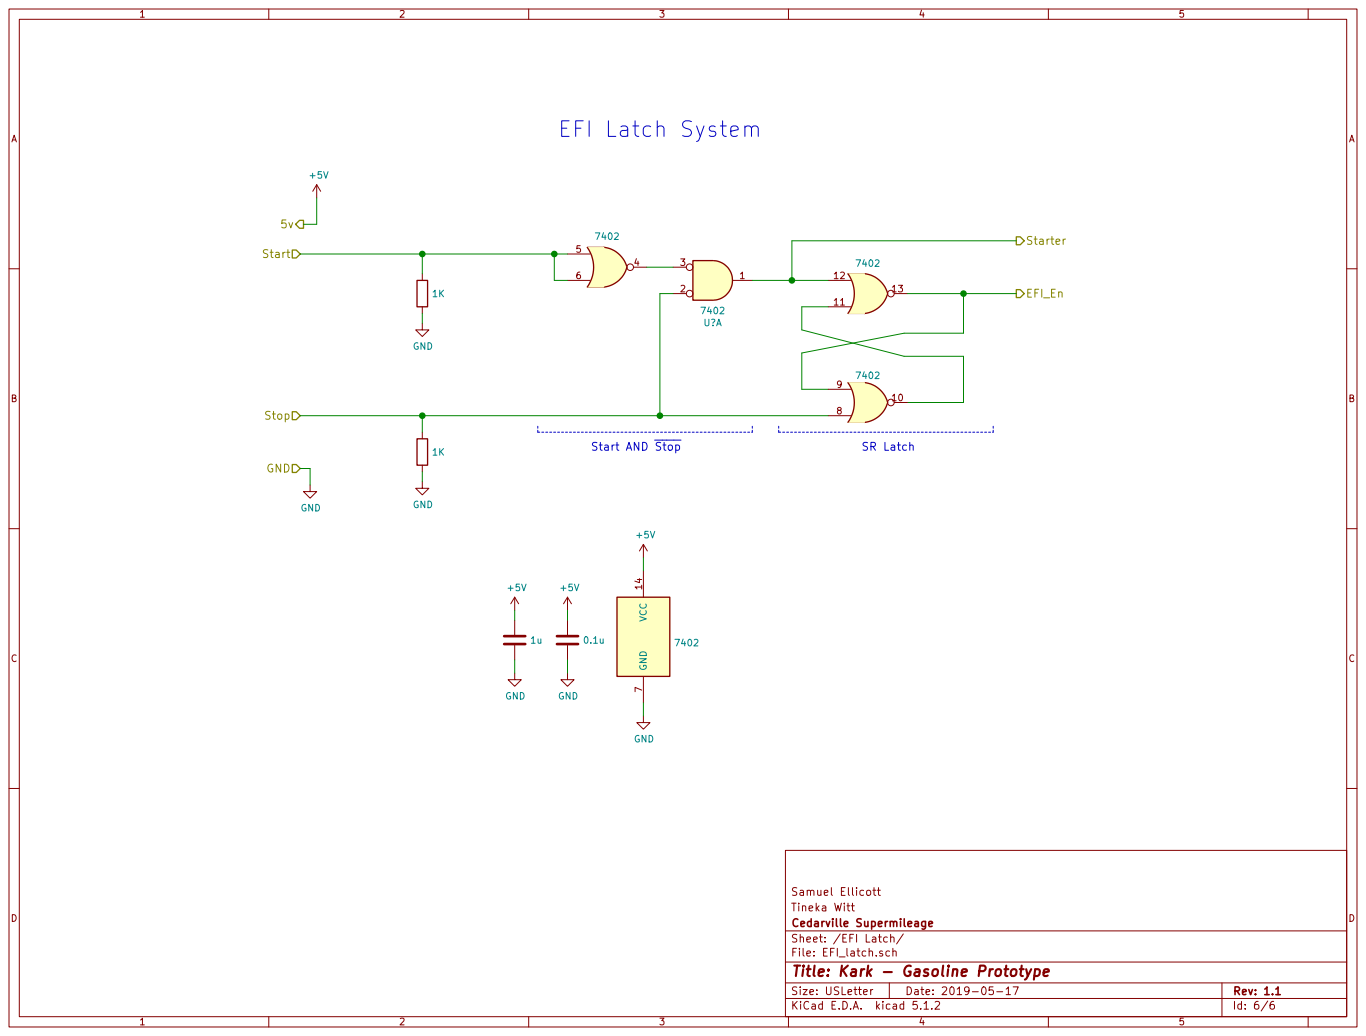
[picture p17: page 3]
D Date: 2019-05-17 KiCad E.D.A. kicad 5.1.2 Size: USLetter; Rev: 1.1; EFI_En; 7402 Start; Stop; Starter +5V GND; Start AND Stop; SR Latch; GND; 1K GND GND; 0.1u +5V GND

7402 VCC ¹⁴ GND

File: EFI_latch.sch Sheet: /EFI Latch/ Cedarville Supermileage Tineka Witt Samuel Ellicott

Id: 6/6 Title: Kark - Gasoline Prototype

# LED1 GND

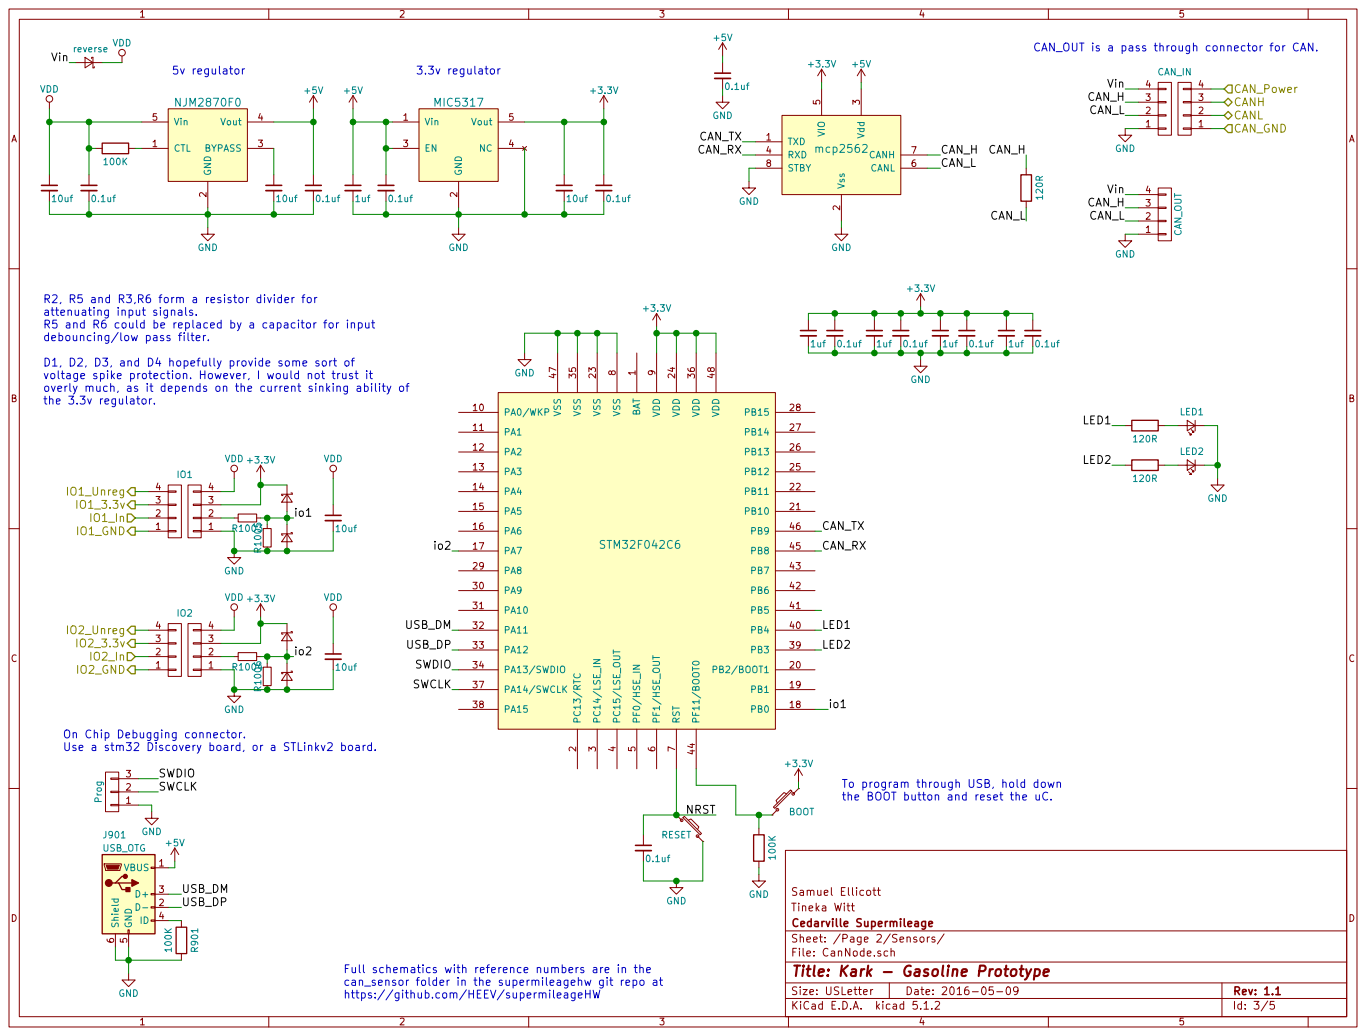
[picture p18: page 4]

CAN_OUT is a pass through connector for CAN.

R2, R5 and R3,R6 form a resistor divider for
attenuating input signals.
R5 and R6 could be replaced by a capacitor for input
debouncing/low pass filter.

D1, D2, D3, and D4 hopefully provide some sort of
voltage spike protection. However, I would not trust it
overly much, as it depends on the current sinking ability of
the 3.3v regulator.

3 PA9 30 PA10 31 PA11 32 PA12 33 PA13/SWDIO 34 VSS 35 VDD 36 PA14/SWCLK 37 PA15 38 PB3 39 PC15/LSE_OUT

On Chip Debugging connector.
Use a stm32 Discovery board, or a STLinkv2 board.

To program through USB, hold down
the BOOT button and reset the uC.

Cedarville Supermileage Tineka Witt Samuel Ellicott

File: CanNode.sch Sheet: /Page 2/Sensors/
Id: 3/5 Title: Kark - Gasoline Prototype

Full schematics with reference numbers are in the can_sensor folder in the supermileagehw git repo at

https://github.com/HEEV/supermileageHW

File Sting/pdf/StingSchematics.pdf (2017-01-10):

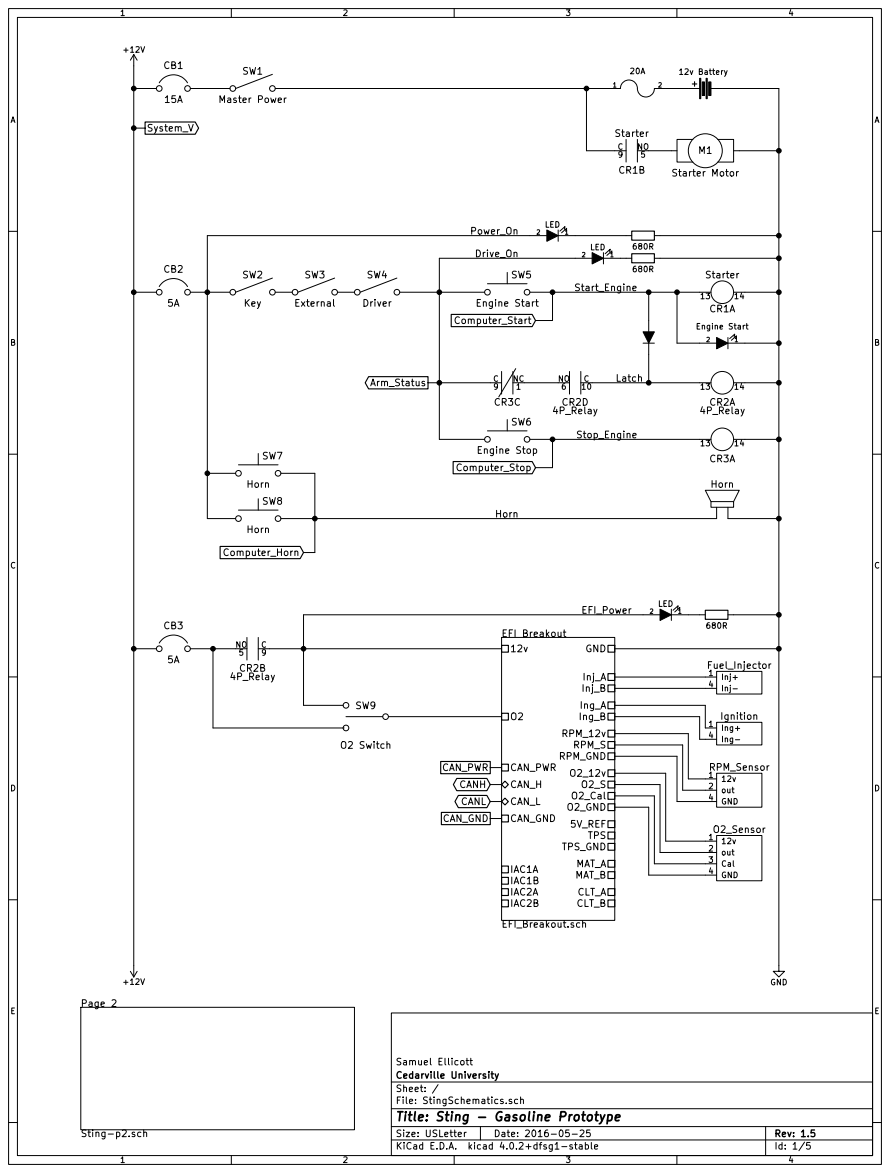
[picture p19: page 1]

File: StingSchematics.sch Sheet: / Cedarville University Samuel Ellicott

Id: 1/5 Title: Sting - Gasoline Prototype

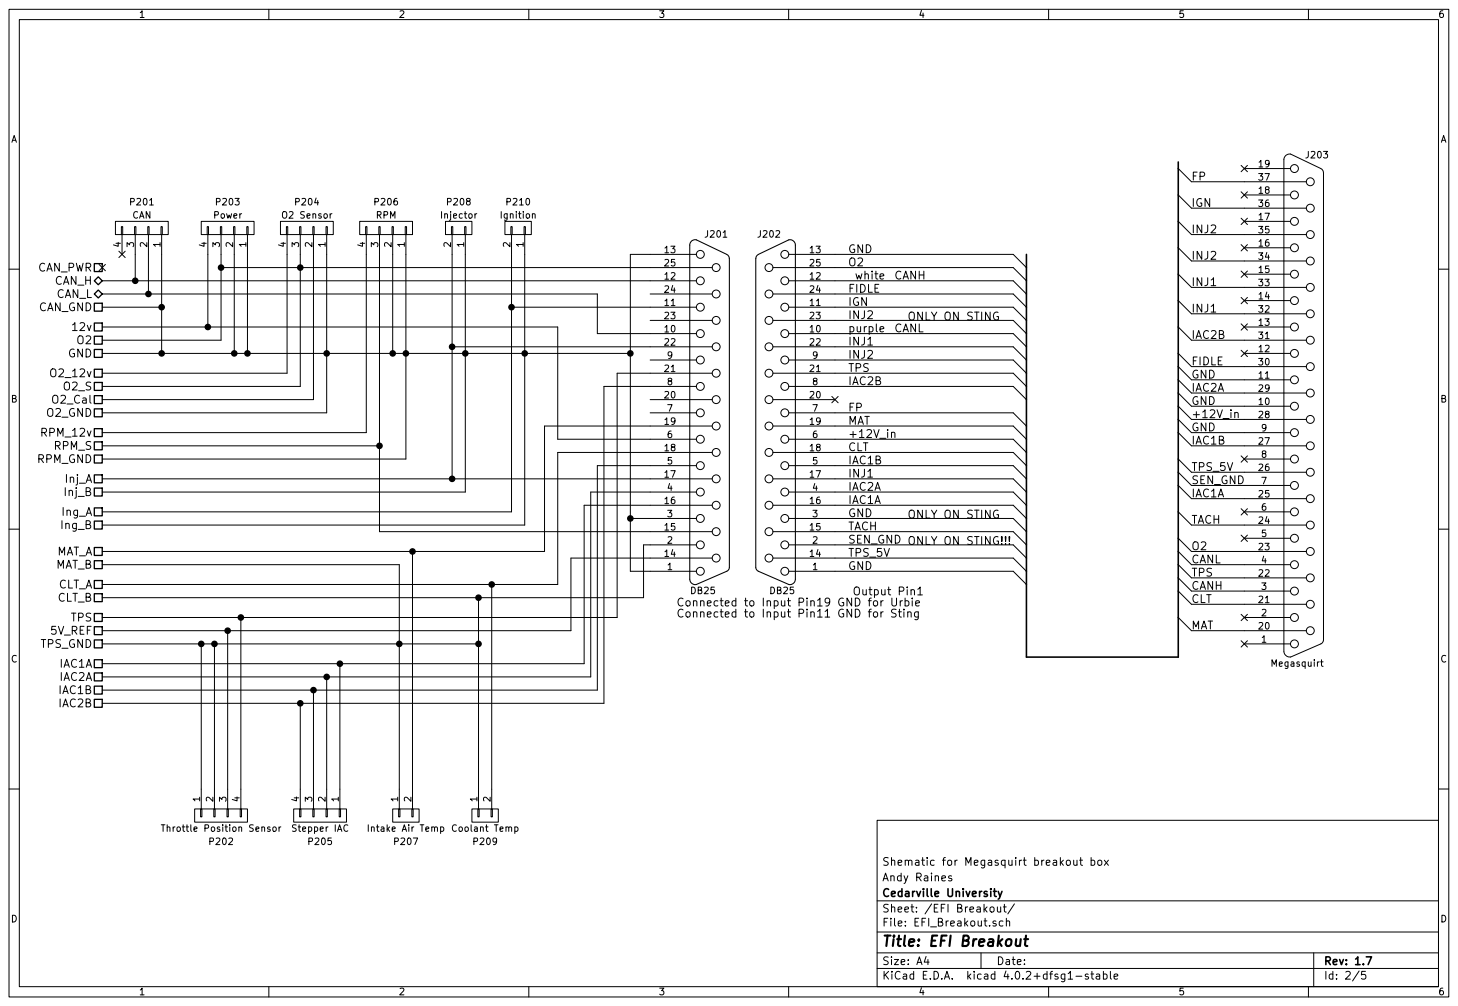
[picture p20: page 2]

2 P209 Coolant Temp MAT CLT

Connected to Input Pin19 GND for Urbie
Connected to Input Pin11 GND for Sting

Shematic for Megasquirt breakout box
Andy Raines
File: EFI_Breakout.sch Sheet: /EFI Breakout/ Cedarville University

Id: 2/5 Title: EFI Breakout

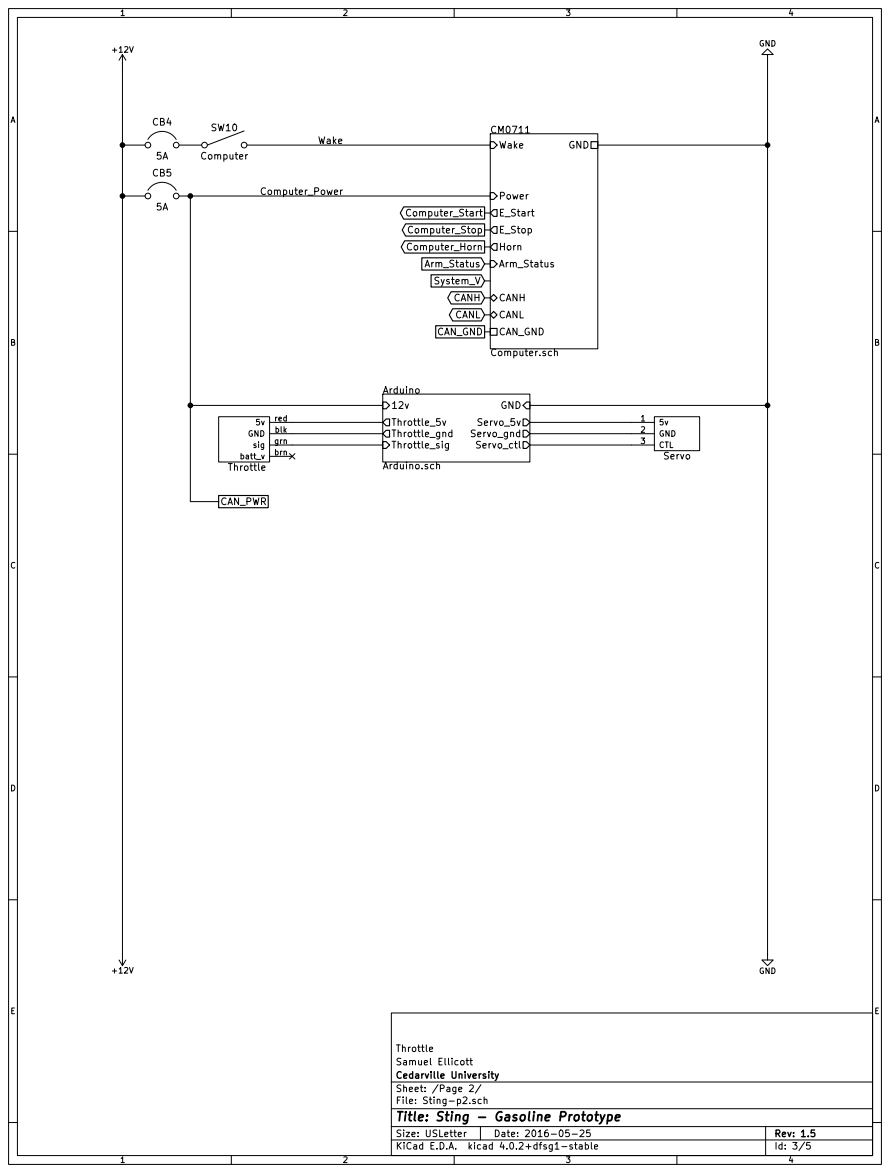
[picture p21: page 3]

Cedarville University Samuel Ellicott Throttle

Sheet: /Page 2/
File: Sting-p2.sch
Id: 3/5 Title: Sting - Gasoline Prototype

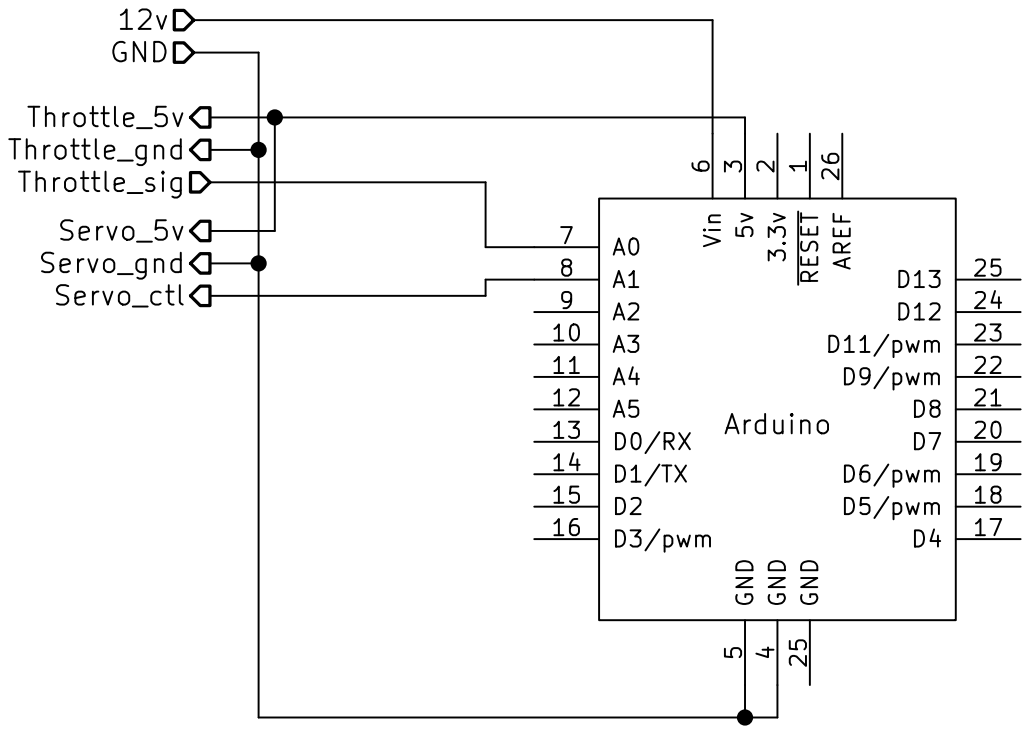
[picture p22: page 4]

6 A0 7 A1 8 A2 9 A3 10 D7 20 A4 11 D8 21 A5 12 D9/pwm 22 D0/RX 13 D11/pwm 23 D1/TX 14 D12 24 D2 15 D13 25 GND 25

1 3.3v 2 5v 3 GND
Cedarville University Samuel Ellicott Arduino wiring connections RESET

File: Arduino.sch Sheet: /Page 2/Arduino/
Id: 4/5 Title: Sting - Gasoline Prototype

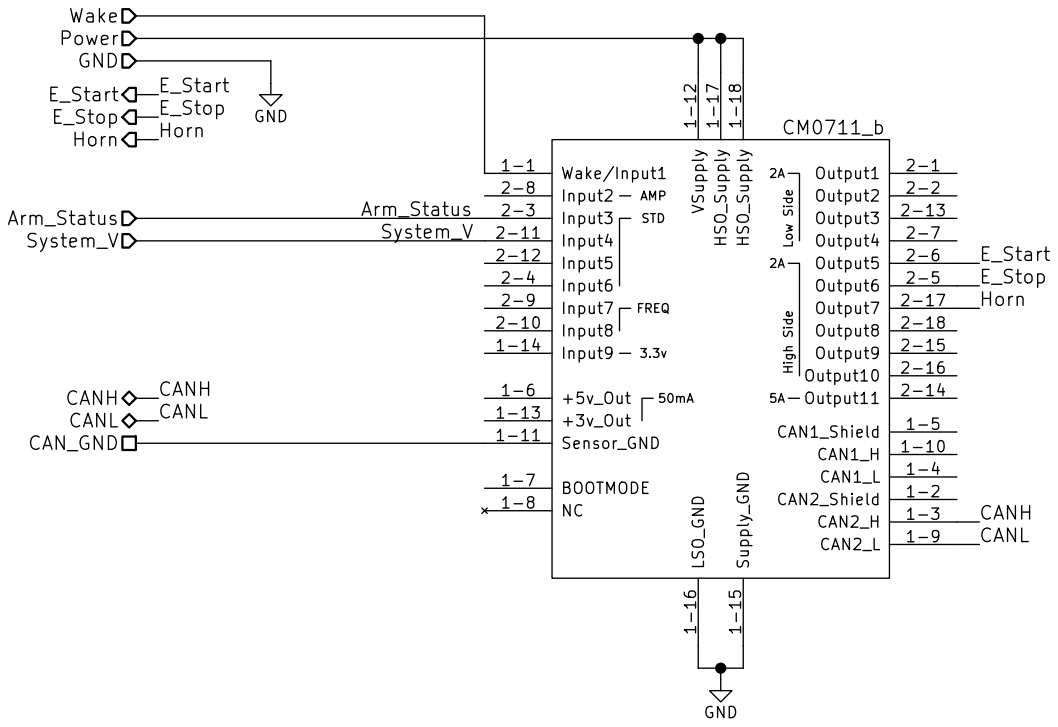
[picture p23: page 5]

Cedarville University Samuel Ellicott schematic for CM0711 computer

Sheet: /Page 2/CM0711/
File: Computer.sch
Id: 5/5 Title: Sting - Gasoline Prototype

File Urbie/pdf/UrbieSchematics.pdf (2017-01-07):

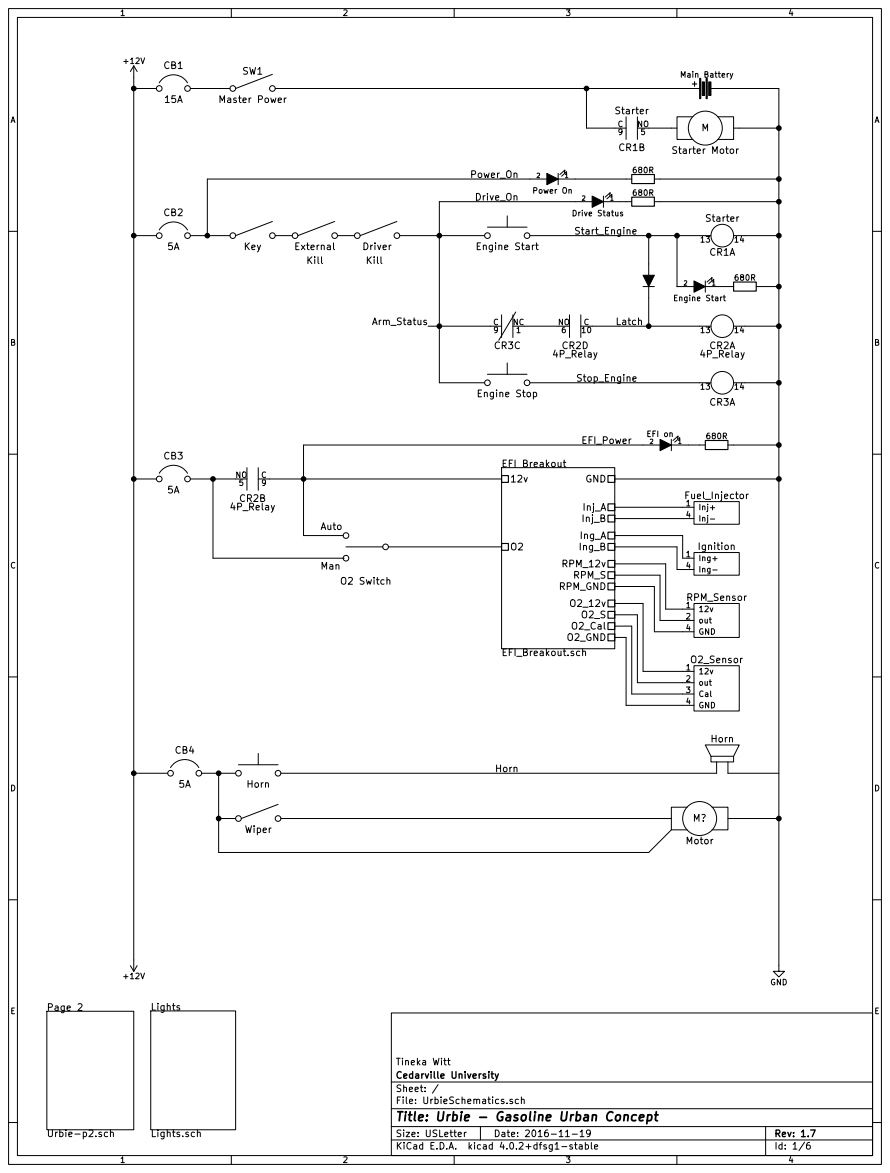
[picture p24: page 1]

Id: 1/6 Title: Urbie - Gasoline Urban Concept File: UrbieSchematics.sch Sheet: / Cedarville University Tineka Witt

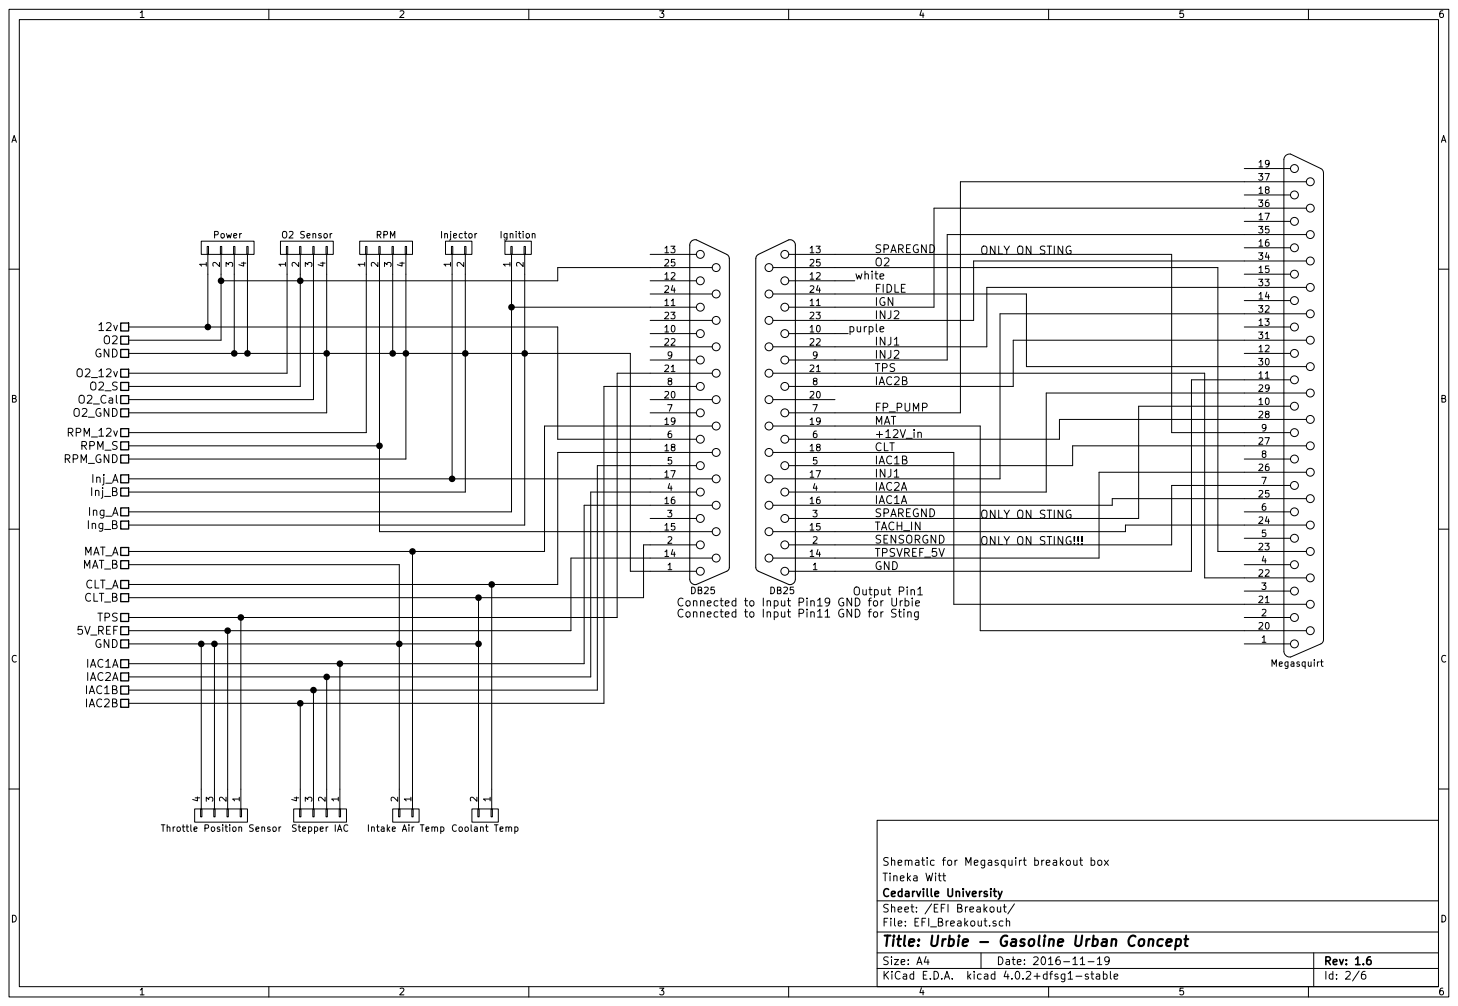
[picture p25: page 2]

25
12 white

11 | IGN

9 | INJ2

8 | IAC2B

10
28
27
8 26

25 6 24 5 23

4 | IAC2A

SENSORGND | | ONLY ON STING!!!

14 | TPSVREF_5V
1 GND

Connected to Input Pin19 GND for Urbie
Connected to Input Pin11 GND for Sting

File: EFI_Breakout.sch Sheet: /EFI Breakout/ Cedarville University Tineka Witt Shematic for Megasquirt breakout box

Id: 2/6 Title: Urbie - Gasoline Urban Concept

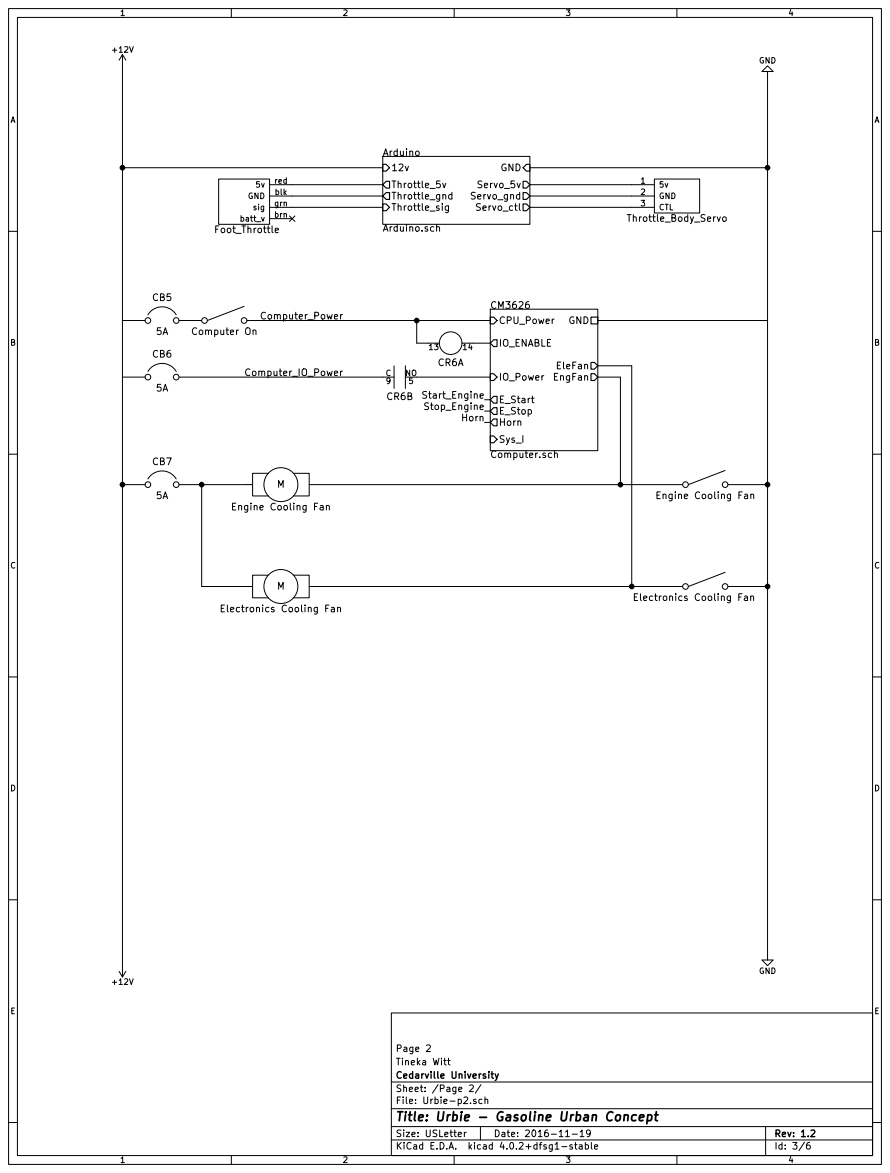
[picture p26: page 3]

Cedarville University Tineka Witt Page 2

Sheet: /Page 2/
File: Urbie-p2.sch
Id: 3/6 Title: Urbie - Gasoline Urban Concept


12v GND
Cedarville University Tineka Witt Arduino wiring connections RESET

6 A0 7 A1 8 A2 9 A3 10 D7 20 A4 11 D8 21 A5 12 D9/pwm 22 D0/RX 13 D11/pwm 23 D1/TX 14 D12 24 D2 15 D13 25 GND 25

Id: 4/6 Title: Urbie - Gasoline Urban Concept File: Arduino.sch Sheet: /Page 2/Arduino/


Cedarville University Tineka Witt schematic for CM3626 computer

Sheet: /Page 2/CM3626/
File: Computer.sch
Id: 5/6 Title: Urbie - Gasoline Urban Concept


9 UrbieLightSwitch
Lf.Turn Park Rt.Turn

Cedarville University Tineka Witt Lights

Sheet: /Lights/
File: Lights.sch
Id: 6/6 Title: Urbie - Gasoline Urban Concept


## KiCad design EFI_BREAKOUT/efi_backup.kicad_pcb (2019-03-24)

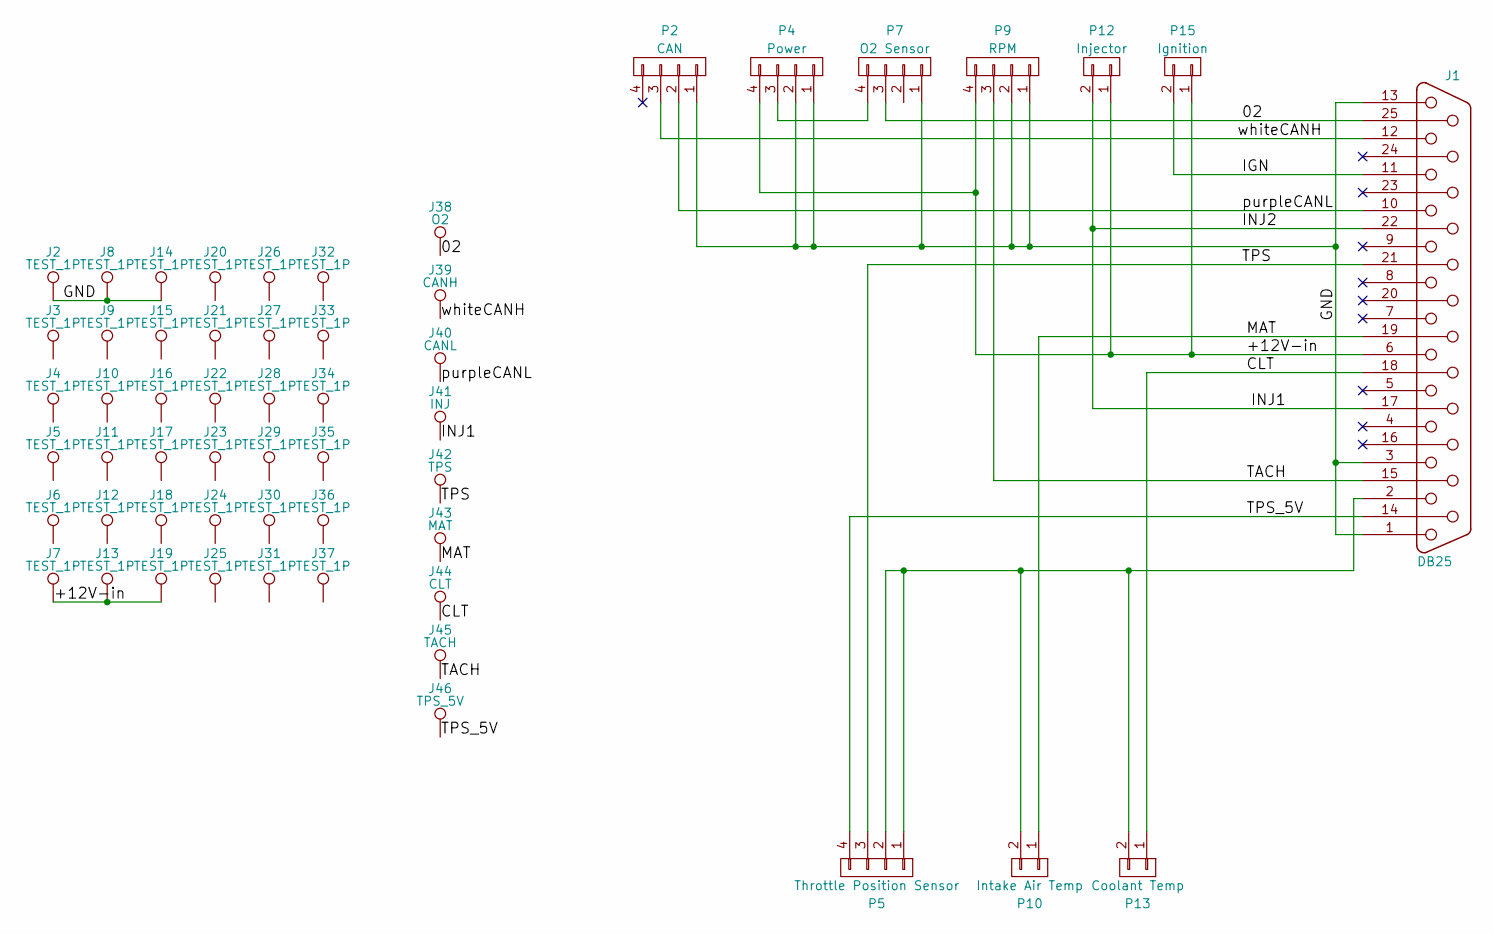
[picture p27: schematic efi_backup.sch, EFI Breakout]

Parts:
J1: DB25; DB25F_CI
J2, J3, J4, J5, J6, J7, J8, J9, J10, J11, J12, J13, J14, J15, J16, J17, J18, J19, J20, J21, J22, J23, J24, J25, J26, J27, J28, J29, J30, J31, J32, J33, J34, J35, J36, J37: TEST_1P; Pin_Header_Straight_1x01_Pitch2.54mm
J38: O2; Pin_Header_Straight_1x01_Pitch2.54mm
J39: CANH; Pin_Header_Straight_1x01_Pitch2.54mm
J40: CANL; Pin_Header_Straight_1x01_Pitch2.54mm
J41: INJ; Pin_Header_Straight_1x01_Pitch2.54mm
J42: TPS; Pin_Header_Straight_1x01_Pitch2.54mm
J43: MAT; Pin_Header_Straight_1x01_Pitch2.54mm
J44: CLT; Pin_Header_Straight_1x01_Pitch2.54mm
J45: TACH; Pin_Header_Straight_1x01_Pitch2.54mm
J46: TPS_5V; Pin_Header_Straight_1x01_Pitch2.54mm
P2: CAN; Pin_Header_Straight_1x01_Pitch2.54mm
P4: Power; Molex-UltraFit-4p
P5: Throttle Position Sensor; Molex-UltraFit-4p
P7: O2 Sensor; Molex-UltraFit-4p
P9: RPM; Molex-UltraFit-4p
P10: Intake Air Temp; Molex-UltraFit-2p
P12: Injector; Molex-UltraFit-2p
P13: Coolant Temp; Molex-UltraFit-2p
P15: Ignition; Molex-UltraFit-2p

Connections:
/02: J1.25, J38.1, P7.3
/+12V-in: J1.6, J7.1, J13.1, J19.1, P4.4, P9.4, P12.1, P15.1
/CLT: J1.18, J44.1, P13.1
/GND: J1.1, J1.3, J1.13, J2.1, J8.1, J14.1, P2.1, P4.1, P4.2, P7.1, P9.1, P9.2
/IGN: J1.11, P15.2
/INJ1: J1.17, J1.22, J41.1, P12.2
/MAT: J1.19, J43.1, P10.1
/TACH: J1.15, J45.1, P9.3
/TPS: J1.21, J42.1, P5.3
/TPS_5V: J1.14, J46.1, P5.4
/purpleCANL: J1.10, J40.1, P2.2
/whiteCANH: J1.12, J39.1, P2.3
unnamed: J1.2, P5.1, P5.2, P10.2, P13.2
unnamed: P4.3, P7.4

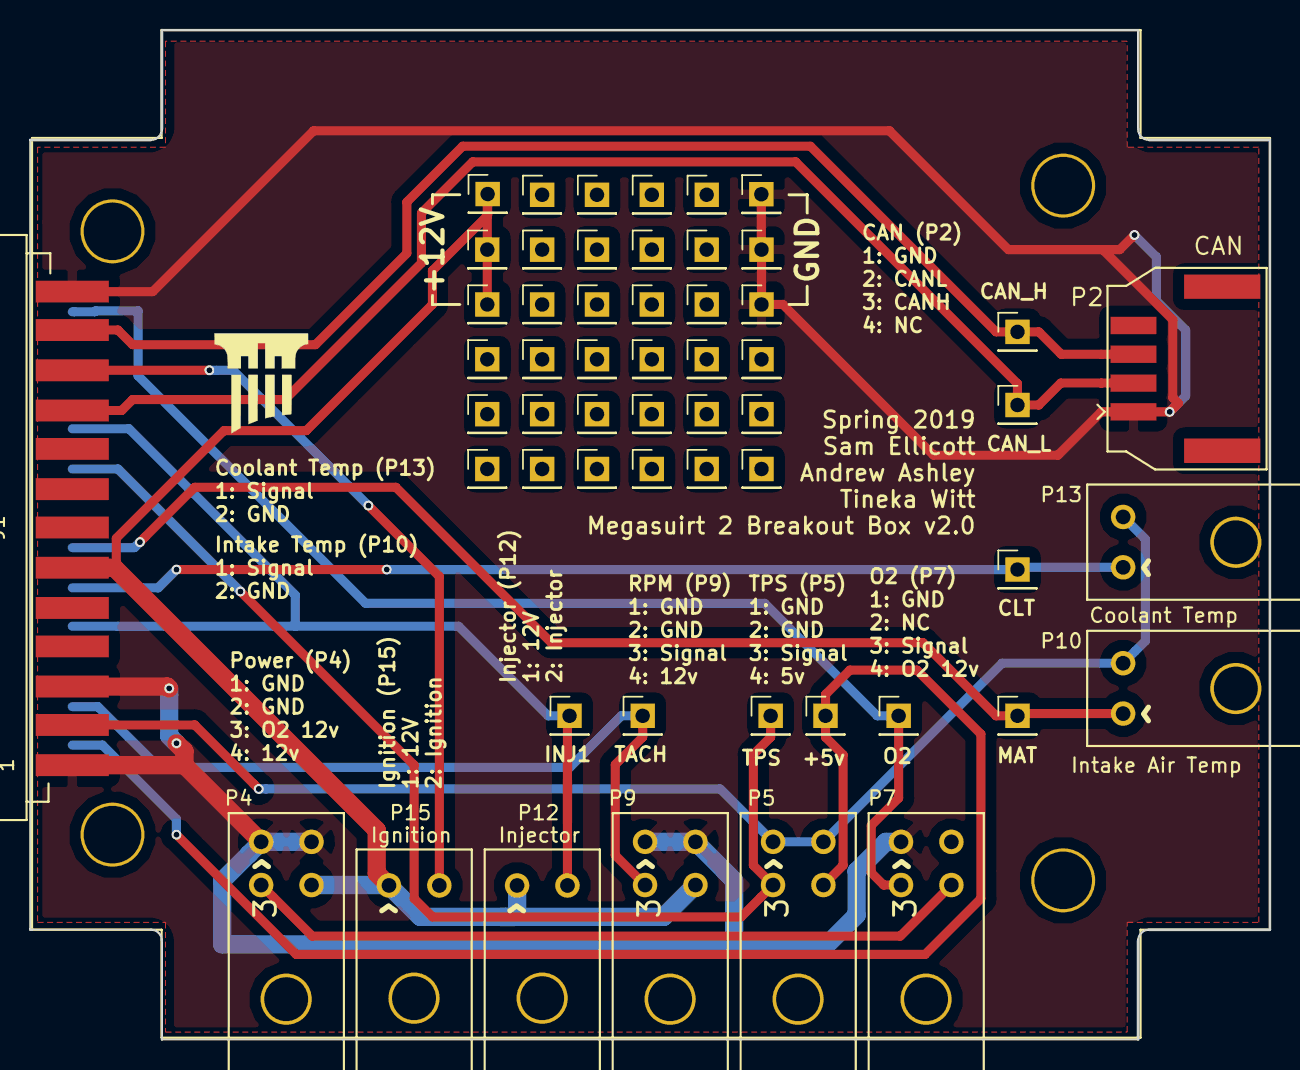
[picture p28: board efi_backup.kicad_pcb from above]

Board: 2 copper layers, 86.1 x 70.1 mm, 55 parts (0 on the bottom side), 14 nets.

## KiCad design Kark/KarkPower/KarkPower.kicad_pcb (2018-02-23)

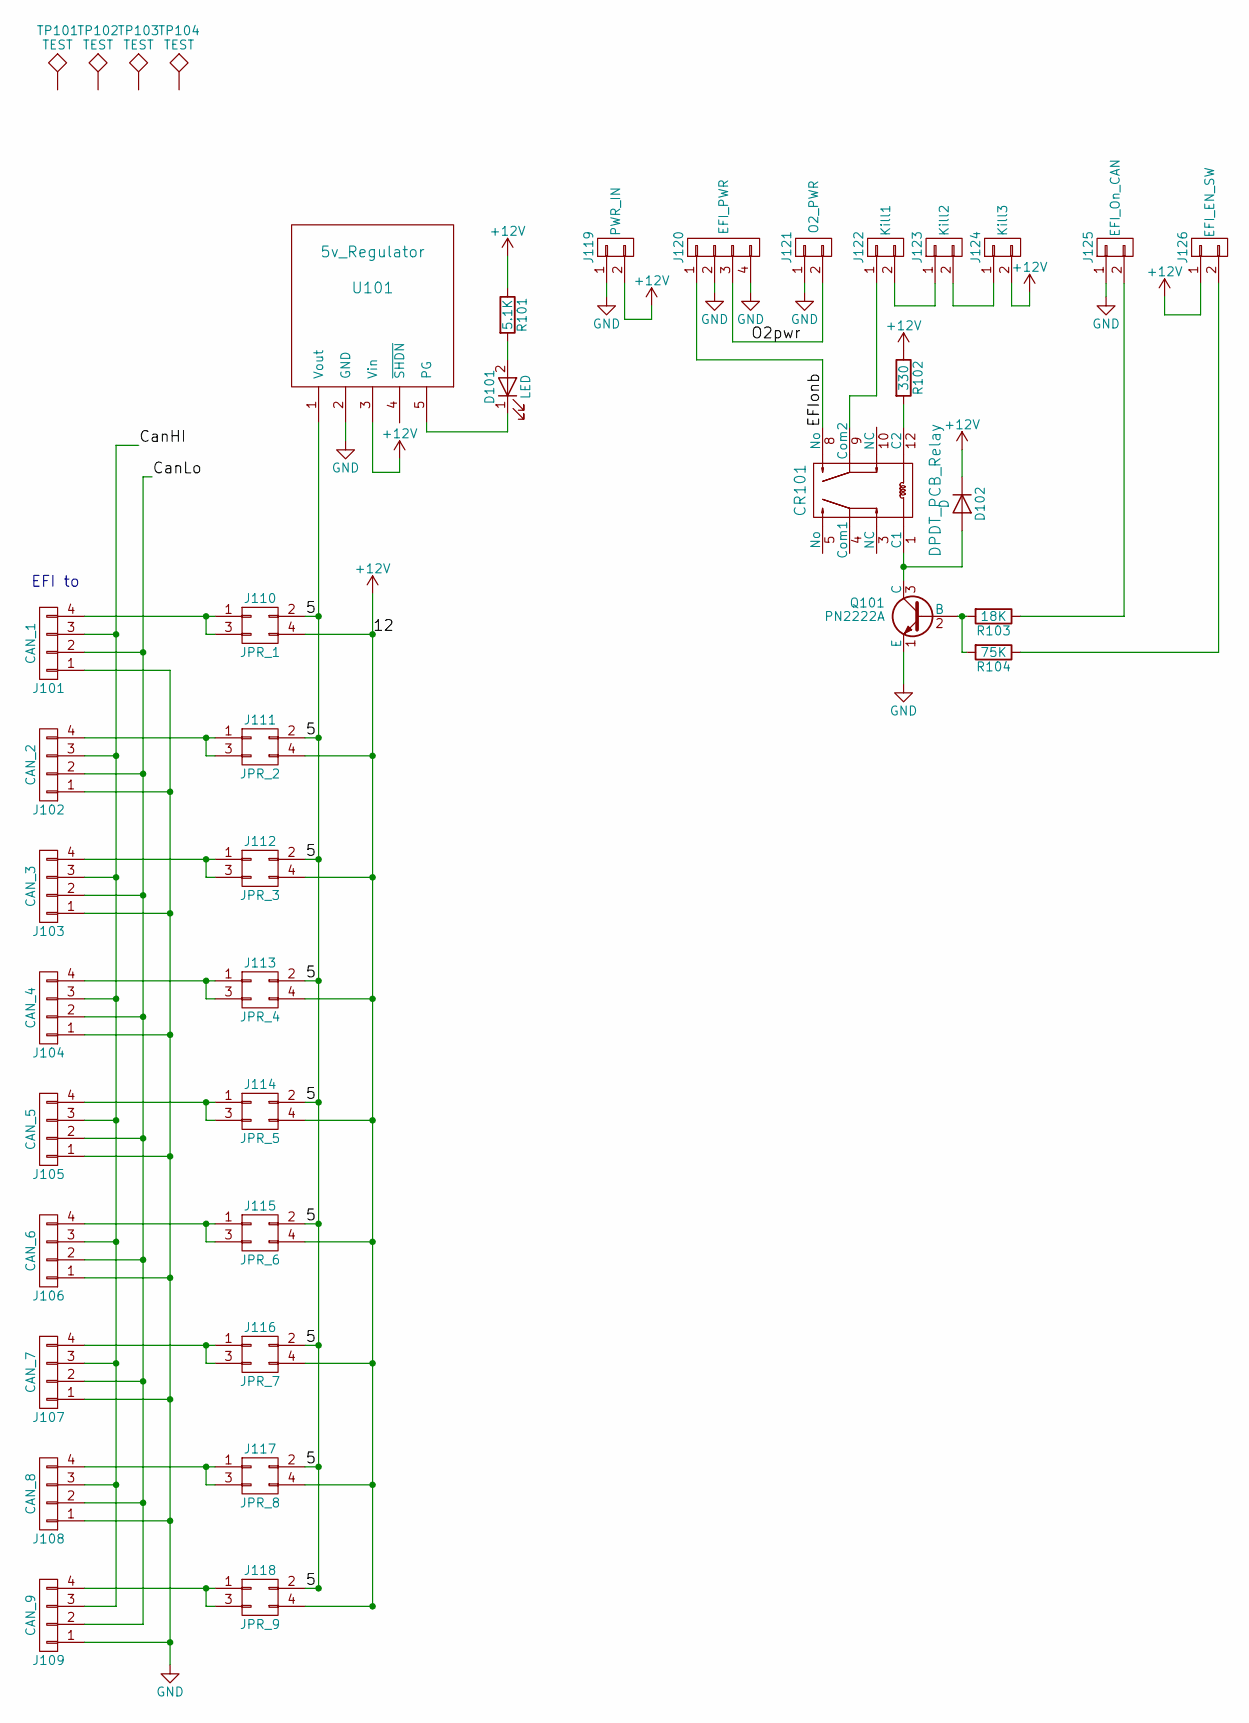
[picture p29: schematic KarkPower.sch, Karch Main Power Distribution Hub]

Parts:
CR101: DPDT_PCB_Relay; 2_FORM_C-RELAY
D101: LED; LED_D3.0mm
D102: D; D_DO-41_SOD81_P7.62mm_Horizontal
J101: CAN_1; Molex-duraClick-4conn
J102: CAN_2; Molex-duraClick-4conn
J103: CAN_3; Molex-duraClick-4conn
J104: CAN_4; Molex-duraClick-4conn
J105: CAN_5; Molex-duraClick-4conn
J106: CAN_6; Molex-duraClick-4conn
J107: CAN_7; Molex-duraClick-4conn
J108: CAN_8; Molex-duraClick-4conn
J109: CAN_9; Molex-duraClick-4conn
J110: JPR_1; Pin_Header_Straight_2x02_Pitch2.54mm
J111: JPR_2; Pin_Header_Straight_2x02_Pitch2.54mm
J112: JPR_3; Pin_Header_Straight_2x02_Pitch2.54mm
J113: JPR_4; Pin_Header_Straight_2x02_Pitch2.54mm
J114: JPR_5; Pin_Header_Straight_2x02_Pitch2.54mm
J115: JPR_6; Pin_Header_Straight_2x02_Pitch2.54mm
J116: JPR_7; Pin_Header_Straight_2x02_Pitch2.54mm
J117: JPR_8; Pin_Header_Straight_2x02_Pitch2.54mm
J118: JPR_9; Pin_Header_Straight_2x02_Pitch2.54mm
J119: PWR_IN; Molex-UltraFit-2p
J120: EFI_PWR; Molex-UltraFit-4p
J121: O2_PWR; Molex-UltraFit-2p
J122: Kill1; Molex-UltraFit-2p
J123: Kill2; Molex-UltraFit-2p
J124: Kill3; Molex-UltraFit-2p
J125: EFI_On_CAN; Molex-UltraFit-2p
J126: EFI_EN_SW; Molex-UltraFit-2p
Q101: PN2222A; TO-92_Inline_Wide
R101: 5.1K; R_Axial_DIN0207_L6.3mm_D2.5mm_P7.62mm_Horizontal
R102: 330; R_Axial_DIN0207_L6.3mm_D2.5mm_P7.62mm_Horizontal
R103: 18K; R_Axial_DIN0207_L6.3mm_D2.5mm_P7.62mm_Horizontal
R104: 75K; R_Axial_DIN0207_L6.3mm_D2.5mm_P7.62mm_Horizontal
TP101, TP102, TP103, TP104: TEST; MountingHole_3.2mm_M3_Pad
U101: 5v_Regulator; D24V10F5

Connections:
+12V: D102.1 (K), J110.4, J111.4, J112.4, J113.4, J114.4, J115.4, J116.4, J117.4, J118.4, J119.2, J124.2, J126.1, R101.1, R102.1, U101.3 (Vin)
/5: J110.2, J111.2, J112.2, J113.2, J114.2, J115.2, J116.2, J117.2, J118.2, U101.1 (Vout)
/CanHI: J101.3, J102.3, J103.3, J104.3, J105.3, J106.3, J107.3, J108.3, J109.3
/CanLo: J101.2, J102.2, J103.2, J104.2, J105.2, J106.2, J107.2, J108.2, J109.2
/EFIonb: CR101.8 (No), J120.1
/O2pwr: J120.3, J121.2
GND: J101.1, J102.1, J103.1, J104.1, J105.1, J106.1, J107.1, J108.1, J109.1, J119.1, J120.2, J120.4, J121.1, J125.1, Q101.1 (E), U101.2 (GND)
unnamed: CR101.1 (C1), D102.2 (A), Q101.3 (C)
unnamed: CR101.9 (Com2), J122.1
unnamed: CR101.12 (C2), R102.2
unnamed: D101.1 (K), U101.5 (PG)
unnamed: D101.2 (A), R101.2
unnamed: J101.4, J110.1, J110.3
unnamed: J102.4, J111.1, J111.3
unnamed: J103.4, J112.1, J112.3
unnamed: J104.4, J113.1, J113.3
unnamed: J105.4, J114.1, J114.3
unnamed: J106.4, J115.1, J115.3
unnamed: J107.4, J116.1, J116.3
unnamed: J108.4, J117.1, J117.3
unnamed: J109.4, J118.1, J118.3
unnamed: J122.2, J123.1
unnamed: J123.2, J124.1
unnamed: J125.2, R103.1
unnamed: J126.2, R104.1
unnamed: Q101.2 (B), R103.2, R104.2

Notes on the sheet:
EFI to

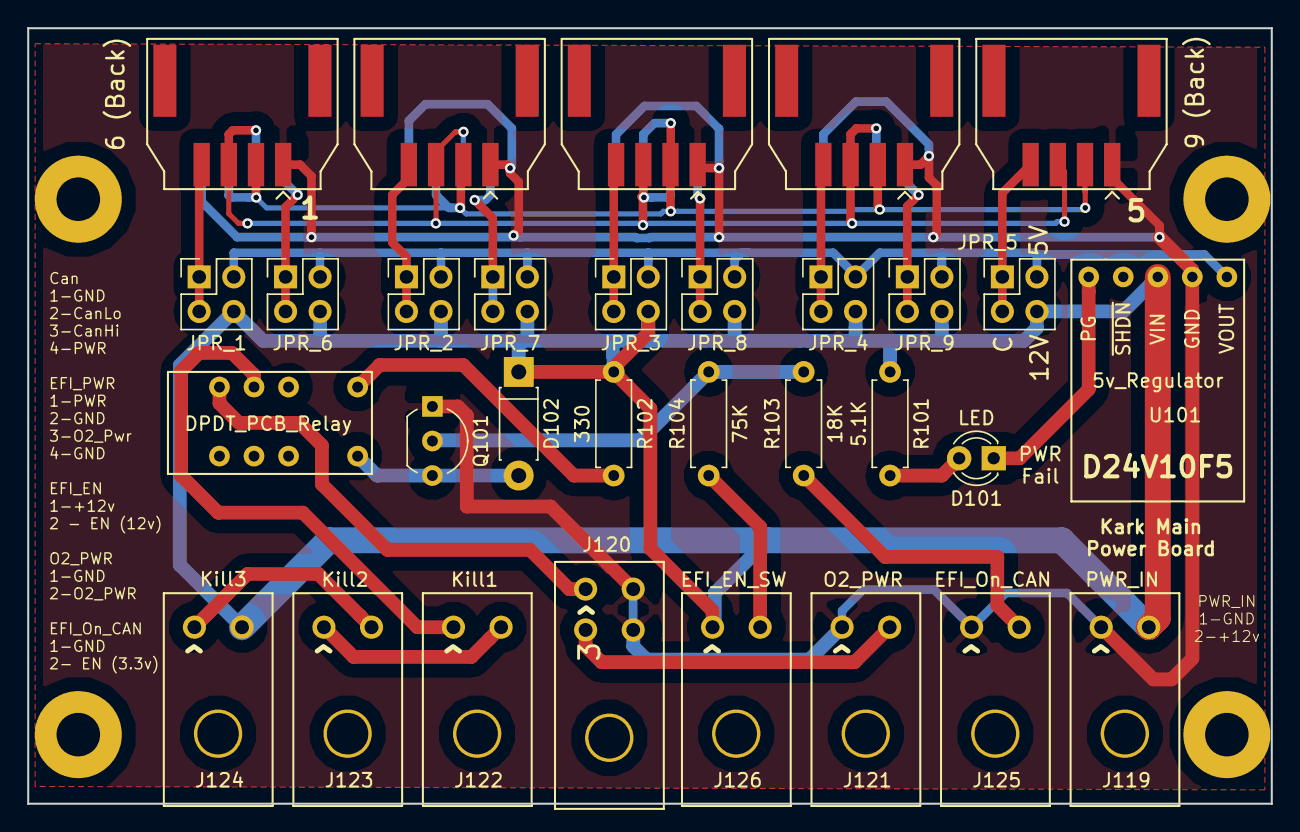
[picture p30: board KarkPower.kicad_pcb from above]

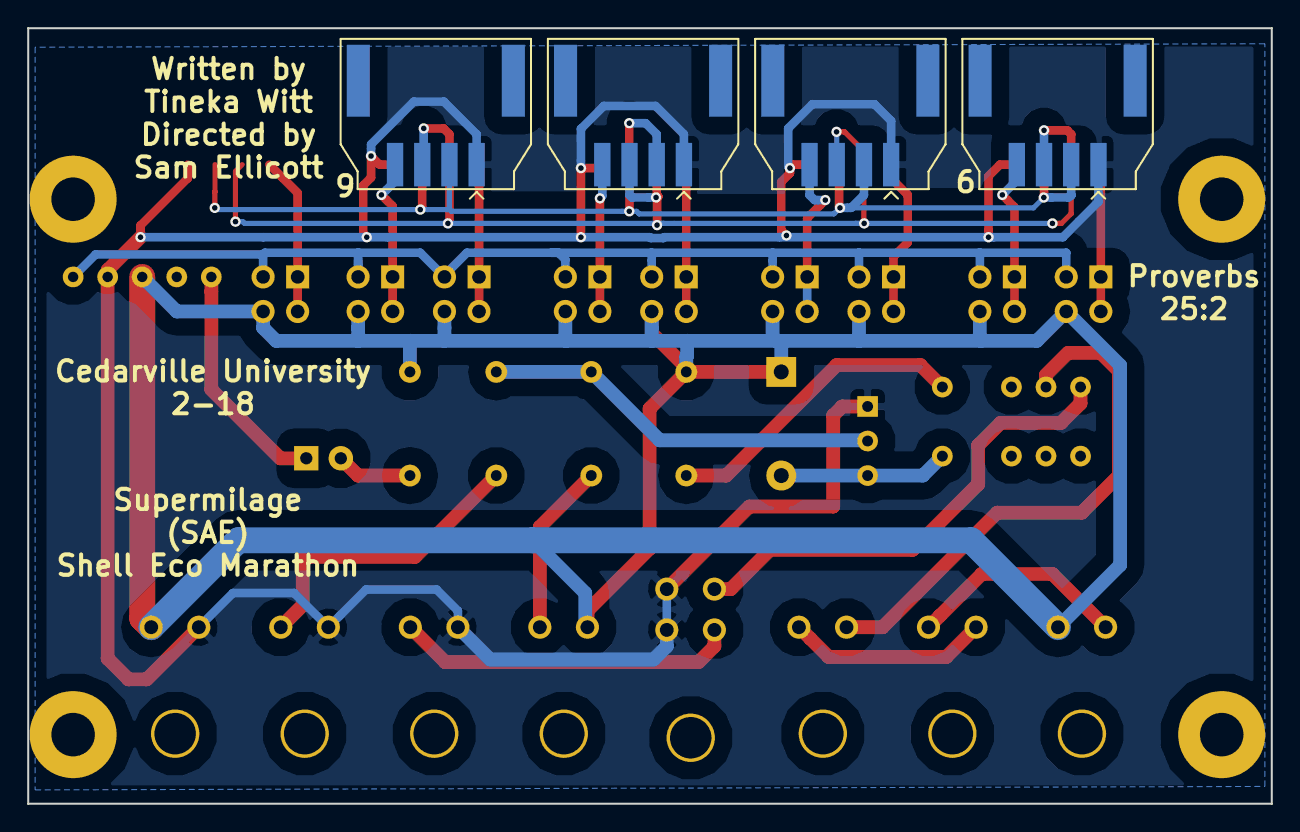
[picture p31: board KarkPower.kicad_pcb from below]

Board: 2 copper layers, 91.4 x 57.0 mm, 39 parts (4 on the bottom side), 26 nets.

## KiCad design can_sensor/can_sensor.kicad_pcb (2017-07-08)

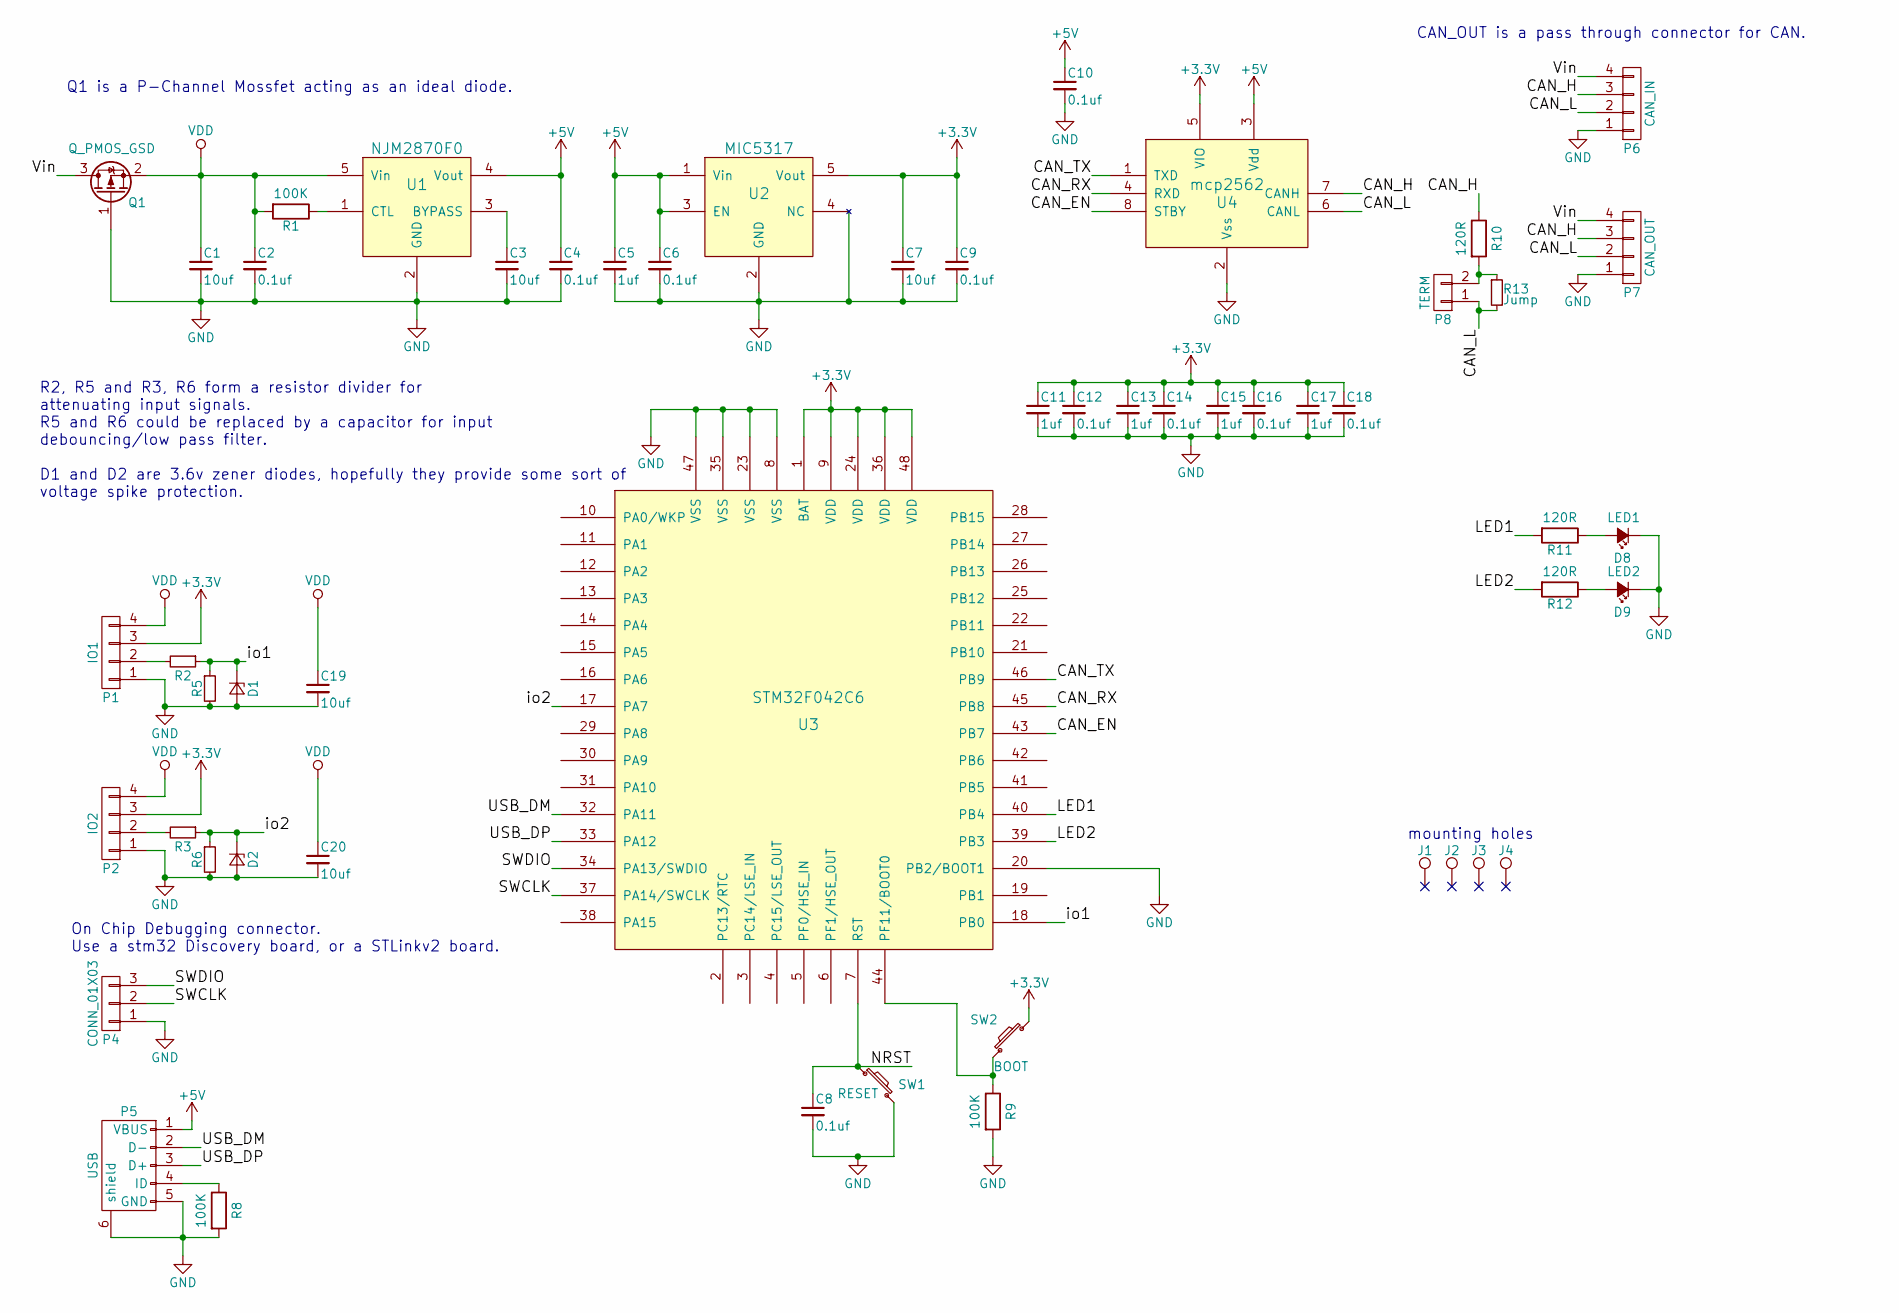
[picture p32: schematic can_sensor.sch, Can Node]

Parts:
C1, C3, C7, C19, C20: 10uf; C_0603_HandSoldering
C2, C4, C6, C8, C9, C10, C12, C14, C16, C18: 0.1uf; C_0603_HandSoldering
C5, C11, C13, C15, C17: 1uf; C_0603_HandSoldering
D1, D2: D_Zener_Small; D_SOD-123
D8: LED1; LED_0603
D9: LED2; LED_0603
J1, J2, J3, J4: TEST_1P
P1: IO1; Molex-duraClick-4conn
P2: IO2; Molex-duraClick-4conn
P4: CONN_01X03; Pin_Header_Straight_1x03
P5: USB; USB_Micro-B
P6: CAN_IN; Molex-duraClick-4conn
P7: CAN_OUT; Molex-duraClick-4conn
P8: TERM; Pin_Header_Straight_1x02_Pitch2.54mm
Q1: Q_PMOS_GSD; SOT-23_Handsoldering
R1, R8, R9: 100K; R_0603_HandSoldering
R2, R3, R5, R6: R; R_0603_HandSoldering
R10, R11, R12: 120R; R_0603_HandSoldering
R13: Jump; R_0603
SW1: RESET; SW_SPST_FSMSM
SW2: BOOT; SW_SPST_FSMSM
U1: NJM2870F0; SOT-23-5
U2: MIC5317; SOT-23-5
U3: STM32F042C6; TQFP-48_7x7mm_Pitch0.5mm
U4: mcp2562; SOIC-8-N

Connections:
+3V3: C7.1, C9.1, C11.1, C12.1, C13.1, C14.1, C15.1, C16.1, C17.1, C18.1, P1.3, P2.3, SW2.1, U2.5 (Vout), U3.1 (BAT), U3.9 (VDD), U3.24 (VDD), U3.36 (VDD), U3.48 (VDD), U4.5 (VIO)
+5V: C4.1, C5.1, C6.1, C10.1, P5.1 (VBUS), U1.4 (Vout), U2.1 (Vin), U2.3 (EN), U4.3 (Vdd)
/CAN_EN: U3.43 (PB7), U4.8 (STBY)
/CAN_H: P6.3, P7.3, R10.1, U4.7 (CANH)
/CAN_L: P6.2, P7.2, P8.1, R13.2, U4.6 (CANL)
/CAN_RX: U3.45 (PB8), U4.4 (RXD)
/CAN_TX: U3.46 (PB9), U4.1 (TXD)
/LED1: R11.2, U3.40 (PB4)
/LED2: R12.2, U3.39 (PB3)
/NRST: C8.1, SW1.1, U3.7 (RST)
/SWCLK: P4.2, U3.37 (PA14/SWCLK)
/SWDIO: P4.3, U3.34 (PA13/SWDIO)
/USB_DM: P5.2 (D-), U3.32 (PA11)
/USB_DP: P5.3 (D+), U3.33 (PA12)
/Vin: P6.4, P7.4, Q1.3 (D)
/io1: D1.1 (K), R2.1, R5.1, U3.18 (PB0)
/io2: D2.1 (K), R3.1, R6.1, U3.17 (PA7)
GND: C1.2, C2.2, C3.2, C4.2, C5.2, C6.2, C7.2, C8.2, C9.2, C10.2, C11.2, C12.2, C13.2, C14.2, C15.2, C16.2, C17.2, C18.2, C19.2, C20.2, D1.2 (A), D2.2 (A), D8.1 (K), D9.1 (K), P1.1, P2.1, P4.1, P5.5 (GND), P5.6 (shield), P6.1, P7.1, Q1.1 (G), R5.2, R6.2, R8.2, R9.2, SW1.2, U1.2 (GND), U2.2 (GND), U2.4 (NC), U3.8 (VSS), U3.20 (PB2/BOOT1), U3.23 (VSS), U3.35 (VSS), U3.47 (VSS), U4.2 (Vss)
unnamed: C3.1, U1.3 (BYPASS)
unnamed: D8.2 (A), R11.1
unnamed: D9.2 (A), R12.1
unnamed: P1.2, R2.2
unnamed: P2.2, R3.2
unnamed: P5.4 (ID), R8.1
unnamed: P8.2, R10.2, R13.1
unnamed: R1.1, U1.1 (CTL)
unnamed: R9.1, SW2.2, U3.44 (PF11/BOOT0)
VDD: C1.1, C2.1, C19.1, C20.1, P1.4, P2.4, Q1.2 (S), R1.2, U1.5 (Vin)

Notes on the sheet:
R2, R5 and R3, R6 form a resistor divider for attenuating input signals. R5 and R6 could be replaced by a capacitor for input debouncing/low pass filter. D1 and D2 are 3.6v zener diodes, hopefully they provide some sort of voltage spike protection.
CAN_OUT is a pass through connector for CAN.
On Chip Debugging connector. Use a stm32 Discovery board, or a STLinkv2 board.
Q1 is a P-Channel Mossfet acting as an ideal diode.
mounting holes

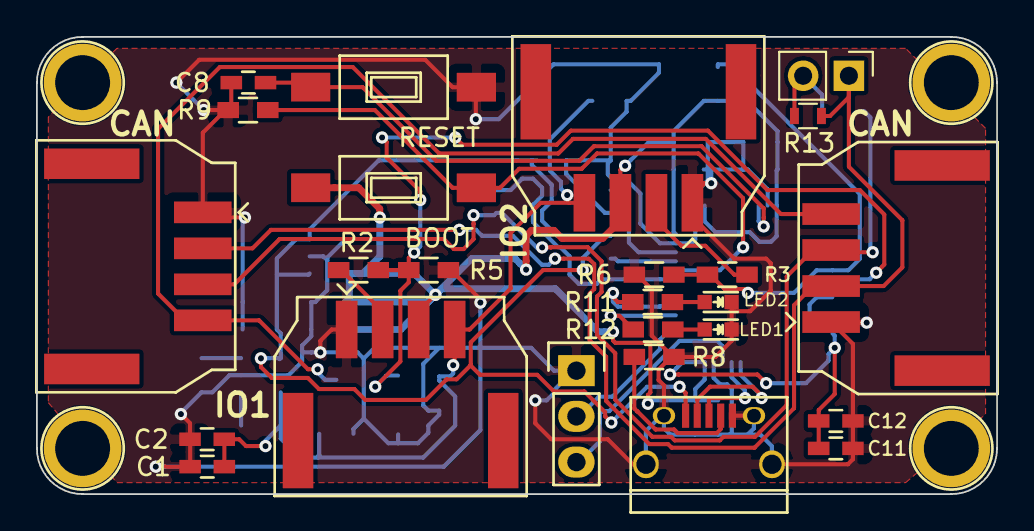
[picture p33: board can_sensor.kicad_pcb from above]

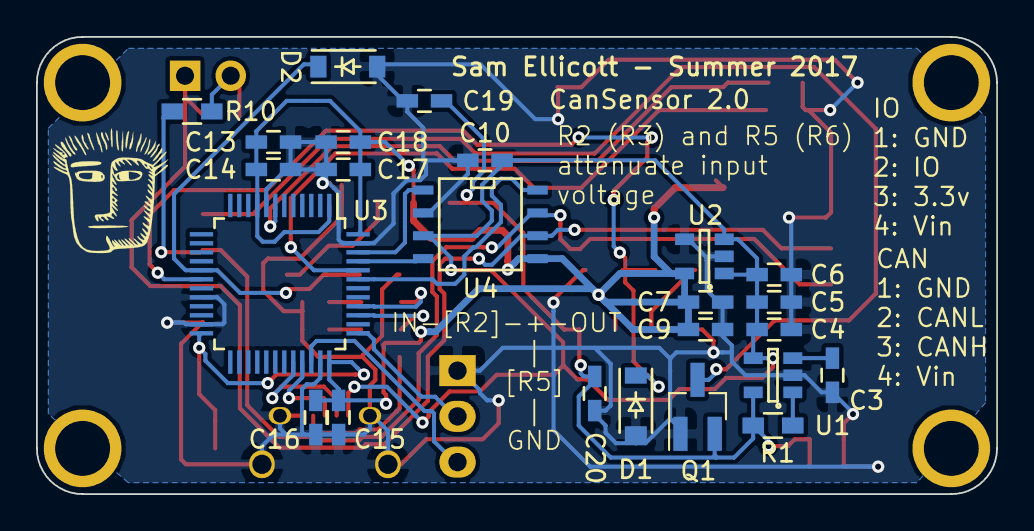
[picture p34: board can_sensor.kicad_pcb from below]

Board: 2 copper layers, 53.3 x 25.4 mm, 49 parts (24 on the bottom side), 28 nets.

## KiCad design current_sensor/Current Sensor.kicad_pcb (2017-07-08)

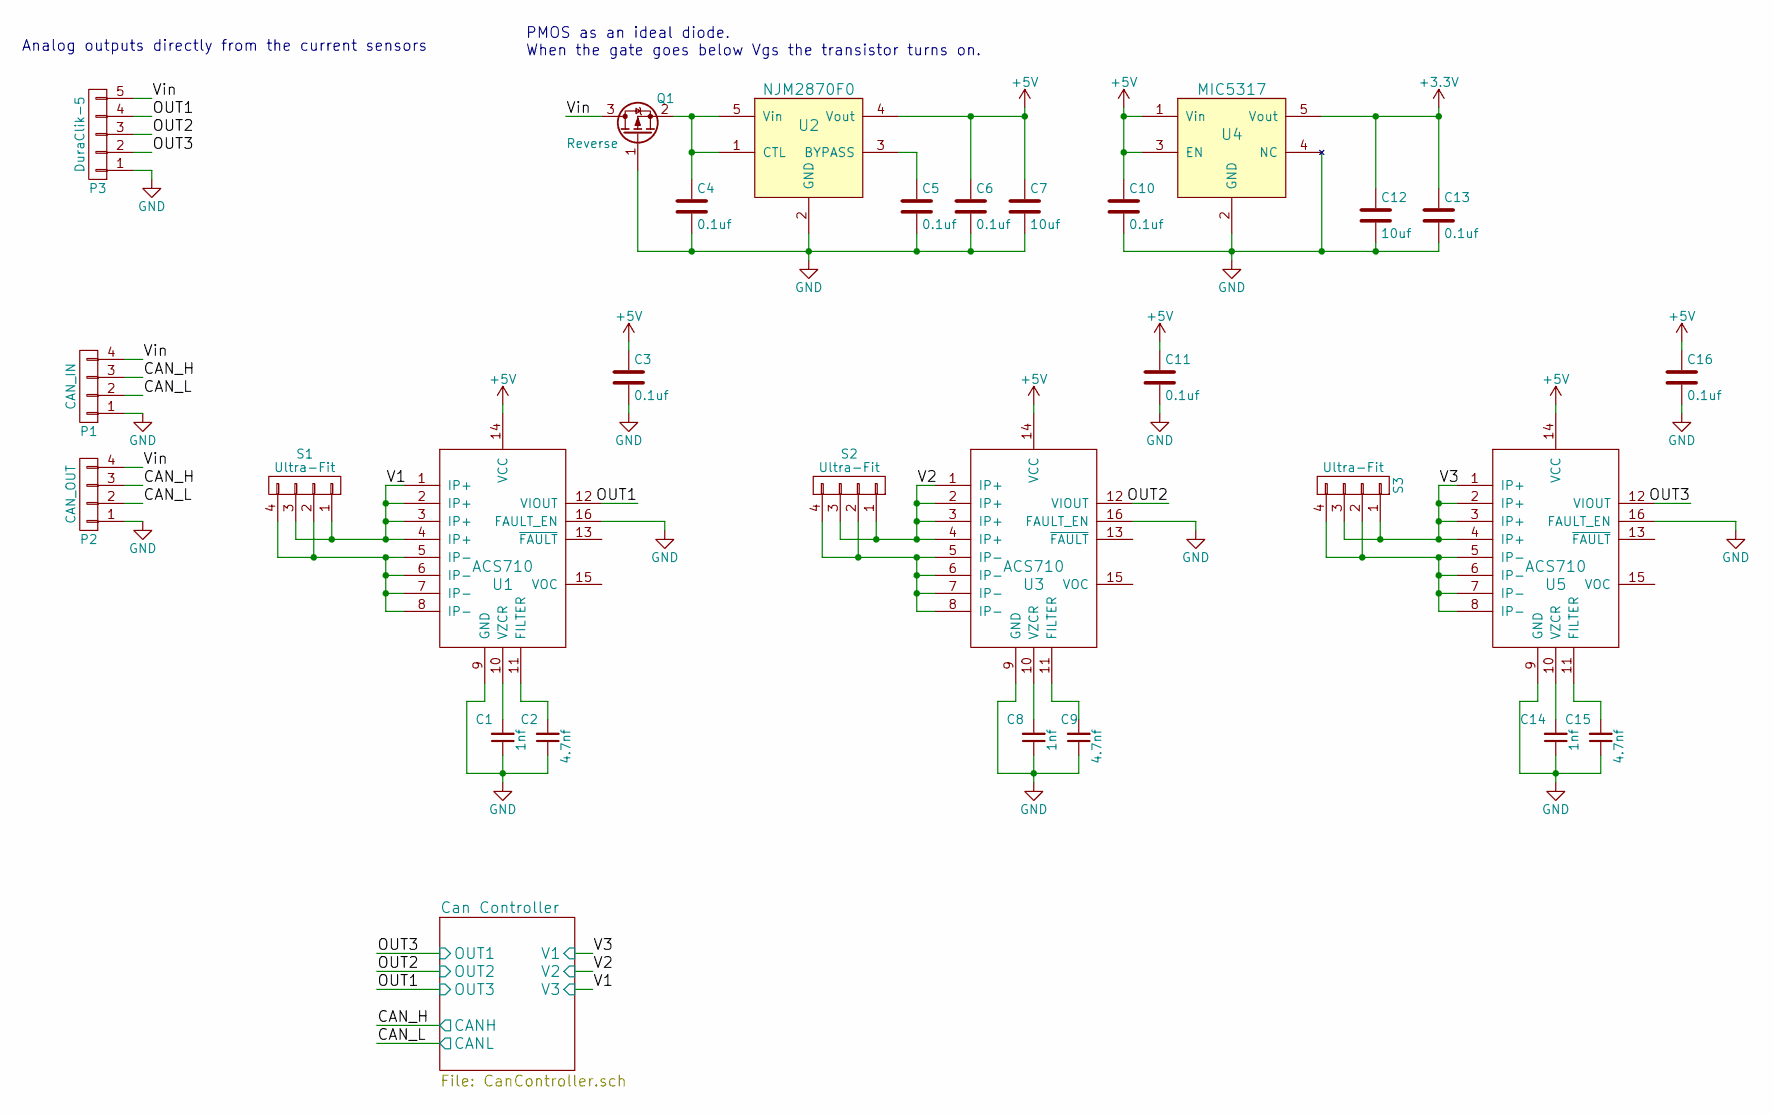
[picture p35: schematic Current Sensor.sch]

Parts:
C1, C8, C14: 1nf; C_0603_HandSoldering
C2, C9, C15: 4.7nf; C_0603_HandSoldering
C3, C4, C5, C6, C10, C11, C13, C16: 0.1uf; C_0603_HandSoldering
C7, C12: 10uf; C_0603_HandSoldering
P1: CAN_IN; Molex-duraClick-4conn
P2: CAN_OUT; Molex-duraClick-4conn
P3: DuraClik-5; Molex-duraClick-5conn
Q1: Reverse; SOT-23_Handsoldering
S1, S2, S3: Ultra-Fit; Molex-UltraFit-4p
U1, U3, U5: ACS710; DIP-16-SchmartBoard
U2: NJM2870F0; SOT-23-5
U4: MIC5317; SOT-23-5

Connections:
+3V3: C12.1, C13.1, U4.5 (Vout); also elsewhere on the board
+5V: C3.1, C6.1, C7.1, C10.1, C11.1, C16.1, U1.14 (VCC), U2.4 (Vout), U3.14 (VCC), U4.1 (Vin), U4.3 (EN), U5.14 (VCC); also elsewhere on the board
/CAN_H: P1.3, P2.3; also elsewhere on the board
/CAN_L: P1.2, P2.2; also elsewhere on the board
/OUT1: P3.4, U1.12 (VIOUT); also elsewhere on the board
/OUT2: P3.3, U3.12 (VIOUT); also elsewhere on the board
/OUT3: P3.2, U5.12 (VIOUT); also elsewhere on the board
/V1: S1.1, S1.3, U1.1 (IP+), U1.2 (IP+), U1.3 (IP+), U1.4 (IP+); also elsewhere on the board
/V2: S2.1, S2.3, U3.1 (IP+), U3.2 (IP+), U3.3 (IP+), U3.4 (IP+); also elsewhere on the board
/V3: S3.1, S3.3, U5.1 (IP+), U5.2 (IP+), U5.3 (IP+), U5.4 (IP+); also elsewhere on the board
/Vin: P1.4, P2.4, P3.5, Q1.3 (D)
GND: C1.1, C2.1, C3.2, C4.2, C5.2, C6.2, C7.2, C8.1, C9.1, C10.2, C11.2, C12.2, C13.2, C14.1, C15.1, C16.2, P1.1, P2.1, P3.1, Q1.1 (G), U1.9 (GND), U1.16 (FAULT_EN), U2.2 (GND), U3.9 (GND), U3.16 (FAULT_EN), U4.2 (GND), U4.4 (NC), U5.9 (GND), U5.16 (FAULT_EN); also elsewhere on the board
unnamed: C1.2, U1.10 (VZCR)
unnamed: C2.2, U1.11 (FILTER)
unnamed: C4.1, Q1.2 (S), U2.1 (CTL), U2.5 (Vin)
unnamed: C5.1, U2.3 (BYPASS)
unnamed: C8.2, U3.10 (VZCR)
unnamed: C9.2, U3.11 (FILTER)
unnamed: C14.2, U5.10 (VZCR)
unnamed: C15.2, U5.11 (FILTER)
unnamed: S1.2, S1.4, U1.5 (IP-), U1.6 (IP-), U1.7 (IP-), U1.8 (IP-)
unnamed: S2.2, S2.4, U3.5 (IP-), U3.6 (IP-), U3.7 (IP-), U3.8 (IP-)
unnamed: S3.2, S3.4, U5.5 (IP-), U5.6 (IP-), U5.7 (IP-), U5.8 (IP-)

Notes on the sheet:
Analog outputs directly from the current sensors
PMOS as an ideal diode. When the gate goes below Vgs the transistor turns on.

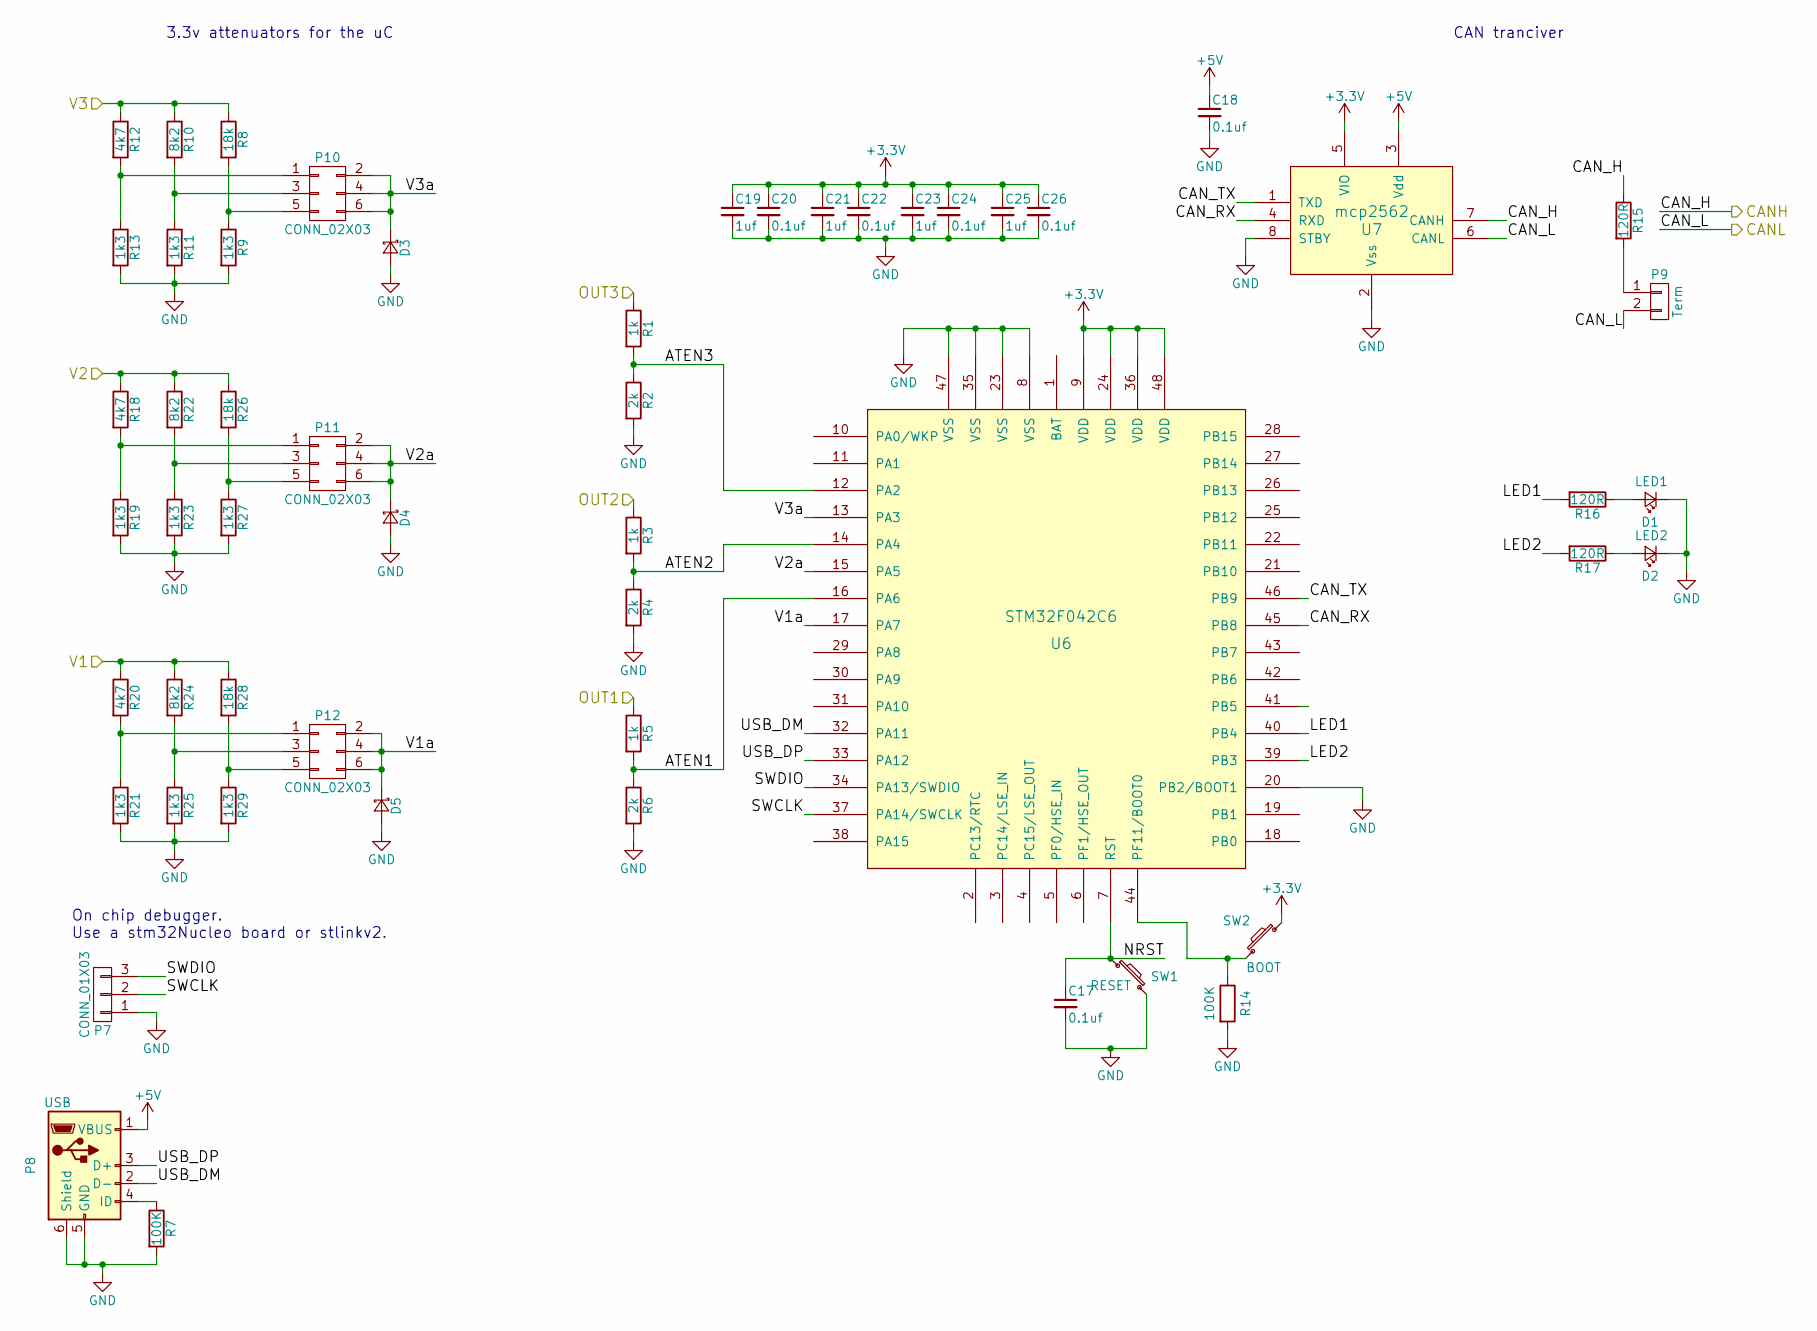
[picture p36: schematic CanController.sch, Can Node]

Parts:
C17, C18, C20, C22, C24, C26: 0.1uf; C_0603_HandSoldering
C19, C21, C23, C25: 1uf; C_0603_HandSoldering
D1: LED1; LED-3MM
D2: LED2; LED-3MM
D3, D4, D5: D_Schottky_Small; SOD-123
P7: CONN_01X03; Pin_Header_Straight_1x03
P8: USB; USB_Micro-B
P9: Term; Pin_Header_Straight_1x02
P10, P11, P12: CONN_02X03; Pin_Header_Straight_2x03
R1, R3, R5: 1k; R_0603_HandSoldering
R2, R4, R6: 2k; R_0603_HandSoldering
R7, R14: 100K; R_0603_HandSoldering
R8, R26, R28: 18k; R_0603_HandSoldering
R9, R11, R13, R19, R21, R23, R25, R27, R29: 1k3; R_0603_HandSoldering
R10, R22, R24: 8k2; R_0603_HandSoldering
R12, R18, R20: 4k7; R_0603_HandSoldering
R15, R16, R17: 120R; R_0603_HandSoldering
SW1: RESET; SW_PUSH_6mm
SW2: BOOT; SW_PUSH_6mm
U6: STM32F042C6; TQFP-48_7x7mm_Pitch0.5mm
U7: mcp2562; SOIC-8-N

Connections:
+3V3: C19.1, C20.1, C21.1, C22.1, C23.1, C24.1, C25.1, C26.1, SW2.1, U6.9 (VDD), U6.24 (VDD), U6.36 (VDD), U6.48 (VDD), U7.5 (VIO); also elsewhere on the board
+5V: C18.1, P8.1 (VBUS), U7.3 (Vdd); also elsewhere on the board
/CAN_H: R15.1, U7.7 (CANH); also elsewhere on the board
/CAN_L: P9.2, U7.6 (CANL); also elsewhere on the board
/Can Controller/ATEN1: R5.2, R6.1, U6.16 (PA6)
/Can Controller/ATEN2: R3.2, R4.1, U6.14 (PA4)
/Can Controller/ATEN3: R1.2, R2.1, U6.12 (PA2)
/Can Controller/CAN_RX: U6.45 (PB8), U7.4 (RXD)
/Can Controller/CAN_TX: U6.46 (PB9), U7.1 (TXD)
/Can Controller/LED1: R16.2, U6.40 (PB4)
/Can Controller/LED2: R17.2, U6.39 (PB3)
/Can Controller/NRST: C17.1, SW1.1, U6.7 (RST)
/Can Controller/SWCLK: P7.2, U6.37 (PA14/SWCLK)
/Can Controller/SWDIO: P7.3, U6.34 (PA13/SWDIO)
/Can Controller/USB_DM: P8.2 (D-), U6.32 (PA11)
/Can Controller/USB_DP: P8.3 (D+), U6.33 (PA12)
/Can Controller/V1a: D5.1 (K), P12.2, P12.4, P12.6, U6.17 (PA7)
/Can Controller/V2a: D4.1 (K), P11.2, P11.4, P11.6, U6.15 (PA5)
/Can Controller/V3a: D3.1 (K), P10.2, P10.4, P10.6, U6.13 (PA3)
/OUT1: R1.1; also elsewhere on the board
/OUT2: R3.1; also elsewhere on the board
/OUT3: R5.1; also elsewhere on the board
/V1: R8.1, R10.1, R12.1; also elsewhere on the board
/V2: R18.1, R22.1, R26.1; also elsewhere on the board
/V3: R20.1, R24.1, R28.1; also elsewhere on the board
GND: C17.2, C18.2, C19.2, C20.2, C21.2, C22.2, C23.2, C24.2, C25.2, C26.2, D1.1 (K), D2.1 (K), D3.2 (A), D4.2 (A), D5.2 (A), P7.1, P8.5 (GND), P8.6 (Shield), R2.2, R4.2, R6.2, R7.2, R9.2, R11.2, R13.2, R14.2, R19.2, R21.2, R23.2, R25.2, R27.2, R29.2, SW1.2, U6.8 (VSS), U6.20 (PB2/BOOT1), U6.23 (VSS), U6.35 (VSS), U6.47 (VSS), U7.2 (Vss), U7.8 (STBY); also elsewhere on the board
unnamed: D1.2 (A), R16.1
unnamed: D2.2 (A), R17.1
unnamed: P8.4 (ID), R7.1
unnamed: P9.1, R15.2
unnamed: P10.1, R12.2, R13.1
unnamed: P10.3, R10.2, R11.1
unnamed: P10.5, R8.2, R9.1
unnamed: P11.1, R18.2, R19.1
unnamed: P11.3, R22.2, R23.1
unnamed: P11.5, R26.2, R27.1
unnamed: P12.1, R20.2, R21.1
unnamed: P12.3, R24.2, R25.1
unnamed: P12.5, R28.2, R29.1
unnamed: R14.1, SW2.2, U6.44 (PF11/BOOT0)

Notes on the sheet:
3.3v attenuators for the uC
CAN tranciver
On chip debugger. Use a stm32Nucleo board or stlinkv2.

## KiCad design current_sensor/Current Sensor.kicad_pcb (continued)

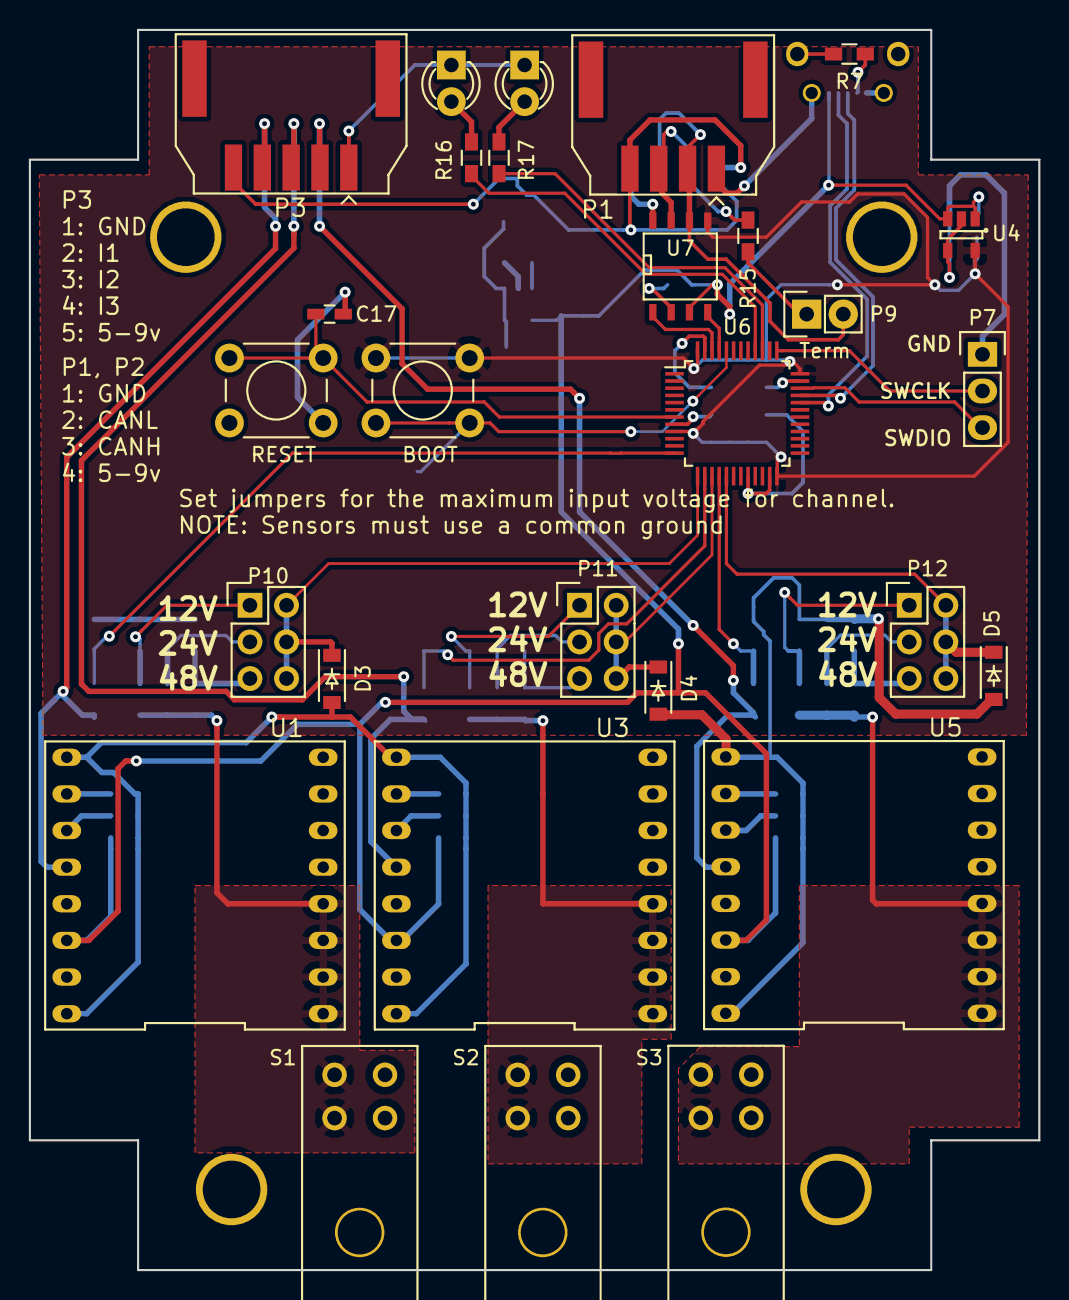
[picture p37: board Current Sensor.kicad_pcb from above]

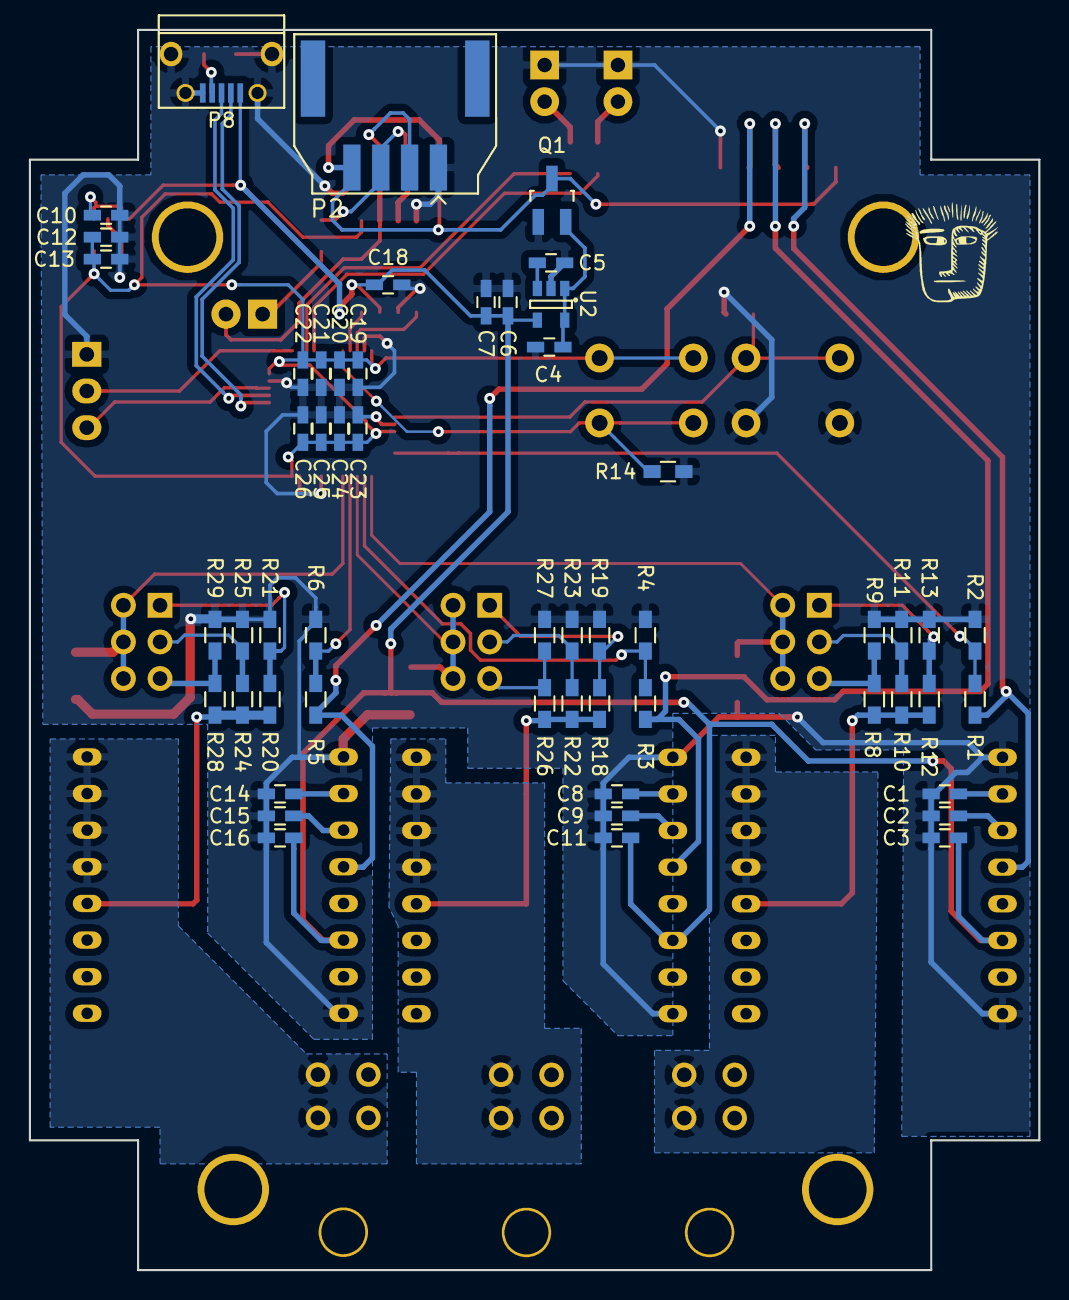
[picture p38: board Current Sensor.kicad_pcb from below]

Board: 2 copper layers, 70.0 x 86.0 mm, 82 parts (54 on the bottom side), 52 nets.

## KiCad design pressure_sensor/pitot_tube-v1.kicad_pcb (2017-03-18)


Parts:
C1, C3, C4, C5, C7: 0.1uf; C_0603_HandSoldering
C2, C6, C8: 10uf; C_0603_HandSoldering
P1: CONN_01X04; Molex-duraClick-4conn
P2: CONN_01X03; Pin_Header_Straight_1x03
Q1, Q2: Q_PMOS_GSD; SOT-23_Handsoldering
R1: 1k; R_0603_HandSoldering
R2: 2k; R_0603_HandSoldering
U1: HSCDRR004MD; DIP-8
U2: NJM2870F0; SOT-23-5
U3: ASDX100A24R
U4: G4V-MINI; Socket_Strip_Straight_1x04
W1, W2, W3, W4: Mount; MountingHole_2.2mm_M2

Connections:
+3V3: C1.1, C2.1, Q2.2 (S), U1.2 (Vcc)
+5V: C5.1, C6.1, C7.1, C8.1, U2.4 (Vout), U3.1 (Vcc), U4.1 (Vcc)
/Out: P1.2, P2.3, R1.1, R2.2, U1.3 (Out)
GND: C1.2, C2.2, C3.2, C4.2, C5.2, C6.2, C7.2, C8.2, P1.1, Q1.1 (G), Q2.1 (G), R2.1, U1.4 (GND), U2.2 (GND), U3.3 (GND), U4.2 (GND)
unnamed: C3.1, Q1.2 (S), U2.1 (CTL), U2.5 (Vin)
unnamed: C4.1, U2.3 (BYPASS)
unnamed: P1.3, Q2.3 (D)
unnamed: P1.4, Q1.3 (D)
unnamed: P2.1, R1.2
unnamed: P2.2, U3.2 (Out), U4.3 (Out)

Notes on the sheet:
Mounting Holes
Comments: Q1 and Q2 are reverse polarity protection transistors. They are P-Channel Mosfets, so they have a very small resistance when on. Care should be taken in their selection so that their V-GS threshold is under 1v U2 is a 5v regulator for the 5v pressure transducer. The output of U3 goes thro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
Molex DuraClik
5v->3.3v Attenuator Select
3.3V differential pressure transducer
5V absolute pressure transducer
5V differential pressure transducer



Board: 2 copper layers, 25.4 x 25.4 mm, 22 parts (7 on the bottom side), 10 nets.

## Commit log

2016-11-26 Added files for can_sensor and current_sensor.
    [CanController.sch, Current Sensor.kicad_pcb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]
2016-11-26 Added pressure sensor folder.
    [pitot_tube-v1.kicad_pcb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]
2016-11-26 moved the currrent sensor to a larger PCB
    [Current Sensor.kicad_pcb, Current Sensor.sch]
2016-11-27 Added all components to the board and finilized placement
    [CanController.sch, Current Sensor.kicad_pcb]
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2016-11-28 added more silkscreen text
    [CanController.sch, Current Sensor.kicad_pcb, Current Sensor.sch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]
2017-01-01 Added Sting schematic files to the repository.
    Fixed random labeling mistakes, added the CM0711 computer, and cleaned
    up the EFI_Breakout page.
    [Arduino.sch, Computer.sch, EFI_Breakout.sch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]
2017-01-02 Added wiring diagrams to the repo.
    There are many changes from the original verion imported, mostly
    related to the computer. The computer was changed from the large CM3626
    to the CM0711. Many other smaller changes were made to increase
    readability.
    [Arduino.sch, Back_Of_Car.sch, Computer.sch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]
2017-01-02 Filled in the Back_Of_Car page more.
    [Arduino.sch, Computer.sch, Sting-p2.sch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]
2017-01-02 Upated Sting schematics to the most recent changes.
    [Arduino.sch, Computer.sch, Sting-p2.sch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]
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2017-01-04 Lots of small changes, major change to the relay box layout.
    Now using busses for the relay box.
    [Arduino.sch, Back_Of_Car.sch, CanNode.sch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]
2017-01-04 Finished cleaning up the relay box wiring diagram.
    [Relay_Box.sch]
2017-01-05 Ah, its finished (I think).
    Added the current sensor board into the wiring diagram, added titles to
    all pages, tried to make everything look pretty.
    [Arduino.sch, Back_Of_Car.sch, CanNode.sch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]
2017-01-05 Changed all page sizes to US Letter size, formatting errors.
    [Arduino.sch, Back_Of_Car.sch, Computer.sch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]
2017-01-05 Added arduino page, small cleanup elsewhere.
    [Arduino.sch, Pressure.sch, Wiring Diagram v2.sch]
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2017-01-05 Added 12v regulator, minor formatting mistakes.
    [Back_Of_Car.sch, Pressure.sch, Wiring Diagram v2.sch]
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2017-01-05 Added fuse before other components.
    [Sting-p2.sch, StingSchematics.sch]
2017-01-05 "Nothing to see here!"
    [Computer.sch, Steering_Wheel.sch]
2017-01-05 Only really tiny formatting stuff.
    [Arduino.sch, Back_Of_Car.sch, CanNode.sch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]
2017-01-06 I'm not really sure what changed
    [Arduino.sch]
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2017-01-06 Added Urbie schematics to repo
    [Arduino.sch, Computer.sch, EFI_Breakout.sch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]
2017-01-06 made the directory layout more sane
    [Arduino.sch, Computer.sch, EFI_Breakout.sch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]
2017-01-06 Organizing relay box sheet
    [FrontHarness.sch, IndicatorLights.sch, LightSwitchConnector.sch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]
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2017-01-07 Added files that changed names
    [FrontLIghts.sch, LightSwitch.sch, SteeringWheel.sch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]
2017-01-18 fixed some stuff
    [Arduino.sch, Back_Of_Car.sch, CanController.sch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]
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2017-03-07 Fixed boot button going to boot1 instead of boot0
    [can_sensor.kicad_pcb, can_sensor.sch]
2017-03-07 Fixed boot button going to boot1 instead of boot0.
    Current sensor board
    [Current Sensor.kicad_pcb]
2017-03-07 Moved to four pin Molex UltraFit connectors.
    Required rearanging layout slightly.
    [Current Sensor.kicad_pcb, Current Sensor.sch]
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2017-03-07 fixed missing parts updated sensor boards
    [Back_Of_Car.sch, CanController.sch, CanNode.sch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]
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2017-06-18 revised CanSensor board to v2.0
    * Jumper to enable and disable 120 Ohm termination resistor
    * IO pin to mcp2562 to enable disable the CAN tranciever
    * Replaced input protection diodes with a zener diode
    * Replaced reverse battery protection diode with a transistor (ideal diode)
    * Better silkscreen comments
    [can_sensor.kicad_pcb, can_sensor.sch]
2017-07-08 updated Current Sensor board with changes made to CanSensor (zener diodes)
    [CanController.sch, Current Sensor.kicad_pcb, Current Sensor.sch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]
2017-09-20 added DPDT switch for Hazard lights on Urbie
    [Arduino.sch, Computer.sch, EFI_Breakout.sch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]
2017-09-23 Wire coloring
    Worked on labeling the color of the wires
    [SwitchPanel.sch, Version1.sch]
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2017-10-01 added a relay to enable the starter relay
    [Arduino.sch, Computer.sch, EFI_Breakout.sch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]
2017-10-02 Moved where the relay to turn on the starter relay gets power from
    [Arduino.sch, Back_Of_Car.sch, CanController.sch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]
2017-12-06 Started project folder Kark
    This contains the master power distrobution pcb outline
    [KarkPower.kicad_pcb, KarkPower.sch, SwitchPanel.sch]
2018-01-13 Karch power prepped for PCB
    Added reisitor values
    Assigned footprints
    small organizational changes
    [KarkPower.sch]
2018-01-20 Started PCB art
    Added mounting pin templates.
    started the PCB first draft.
    [_saved_KarkPower.sch]
2018-01-20 EFI Breakout
    Changed Ignition and Injection GND wires to power
    [efi_backup.sch]
2018-01-20 EFI Breakout
    Added extra "bread board test pins"
    [efi_backup.sch]
2018-01-20 PCB Developed Further
    Organized and optimized part layout.
    (wires not started)
    [KarkPower.kicad_pcb, KarkPower.sch, _saved_KarkPower.sch]
2018-01-27 Kark Power PCB tracks developed
    The PCB tracks were developed and laid with default thicknesses for the main systems.
    [KarkPower.kicad_pcb]
2018-01-27 Karch PCB
    Critical Wires Thickened some Silk Screen added.
    [KarkPower.kicad_pcb]
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2018-02-03 Finishing touches on Kark Power
    Added Silk screen
    Fixed some bugs
    [KarkPower.kicad_pcb]
2018-02-03 Plotted PCB,Drill File
    Created the files in question
    [KarkPower.kicad_pcb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]
2018-02-10 Fitted board to box
    Slightly changed dimentions, tracings and text to fit the selected electrical box
    [KarkPower.kicad_pcb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]
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2018-02-10 Visual formatting
    Moved silk screen to avoid confliction
    caused part numbers on the protoype area to not appear in silkscreen
    Updated the footprints to with pin designators in the silkscreen.
    [efi_backup.kicad_pcb]
2018-02-10 Final Formatting for production
    Edited text and added labeles.
    Added power and ground on the test area.
    Updated authors and year.
    [efi_backup.kicad_pcb, efi_backup.sch]
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2018-03-17 Integrated Power Board layout
    Added the schematic version of the content of the Power Board PCB.
    Added an extra battery for the Engine.
    Changed enables from copy of Sting system to regulation.
    [KarkPower.sch, KarkSchematics.sch]
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2018-03-24 Schematic corrections
    Corrected wiring for fuel pump and moved the EFI chip over to accomodate the change
    [KarkSchematics.sch]
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2018-03-24 Kark Schematic additions
    Fixed fuel pump
    Added wheel sheetand digital switches
    [CM711.sch, KarkPower.sch, KarkSchematics.sch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]
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2018-03-24 Created can breakout
    Added can boards fro sensors and integrated the computer to the can system.
    Created the Can powering system.
    [CM711.sch, CanNode.sch, KarkPower.sch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]
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
